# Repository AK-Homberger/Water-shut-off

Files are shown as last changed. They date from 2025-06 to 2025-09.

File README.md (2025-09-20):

# Water leakage detection and shut-off with ZigBee and ioBroker

A water damage following a burst pipe or other leak is always unpleasant. Especially when it happens while you're on vacation and no one notices the damage, but the water just keeps flowing. A simple project to shut off the house's water supply when a leak is detected can help. The detection is done with the Ikea BADRING water detector, and the shut-off is done with a 12-volt cordless screwdriver controlled by an Ikea TRETAKT switch. I implemented the logic and alarm system using the ioBroker smart home system and the ZigBee software Zigbee2MQTT. ioBroker also sends notifications via email and calls to your mobile phone. 

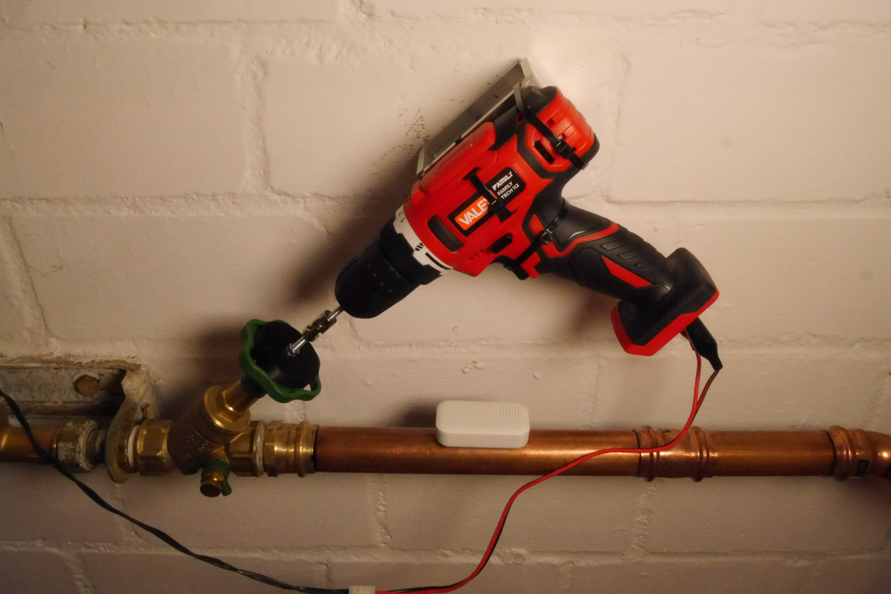
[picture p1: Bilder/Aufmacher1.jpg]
Shut-off


# Summary
- Domestic water shut-off via cordless screwdriver with torque adjustment 
- Leakage detection via Ikea ZigBee water detector BADRING 
- Control of the cordless screwdriver via Ikea ZigBee switch TRETAKT 
- Any number of sensors can be integrated 
- Adapter plate for handwheel as 3D printing template (customisable) 
- Cardan joint as axis shift compensation 
- Alerts via email and phone call (requires Fritzbox) 
- Control via script in IoBroker on a Raspberry 
- ZigBee integration in ioBroker via Zigbee2MQTT 

# Hardware
For the mechanical shut-off of the domestic water, I use a simple 12-volt hand drill with a torque setting. I had initially considered using a gear motor. But I couldn't find the necessary torque clutch anywhere at a reasonable price. It's standard on cordless drills, however. The [list of parts](https://github.com/AK-Homberger/Wasserabschalter/blob/main/README.md#sources) includes a link to [Amazon](https://www.amazon.de/Akkuschrauber-Lithium-family-tech-112-Valex-1429400/dp/B077YSQW1Z). A simple drill for less than €20 is sufficient here.

Here is a short [video](https://www.dropbox.com/scl/fi/2sde03j0u3wew94bmh6hg/Abschalter.mov?rlkey=7kxjaejoa726u7x39rb6fkuw9&dl=0), that shows the function.

The drill is connected to the water valve's handwheel via a universal joint and an adapter plate. The universal joint is designed to compensate for slight axis shifts. It would probably work without this joint as well.

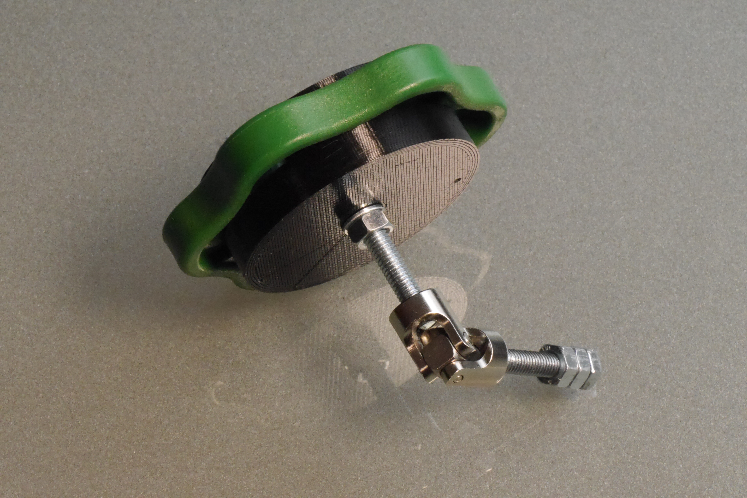
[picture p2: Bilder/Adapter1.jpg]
Adapter


The adapter plate and mounting ring are available in the SCAD directory as OpenSCAD and STL files. The adapter plate should fit for most handwheels. However, if necessary, the plate can easily be adapted to the current handwheel using [OpenSCAD](https://openscad.org/). 

Adapter plate / Ring

### Important! Non-rising spindle
The shut-off only works with valves with a ["non-rising"](https://www.youtube.com/watch?v=0fCbAA_am2k) spindel/stem. With valves with a "rising" spindle, the handwheel shaft rotates into the valve when shutting off. This would cause the distance to the drill to steadily increase until there is no longer any connection. Therefore, check beforehand whether a valve with a "non-rising" spindle is installed. The valves/upper parts can also be easily replaced. Your local plumber can help with this if necessary.

To easily mount the cordless screwdriver, I use so-called [Thermohalter](https://alufensterbaenke.de/thermohalter) for window sills.

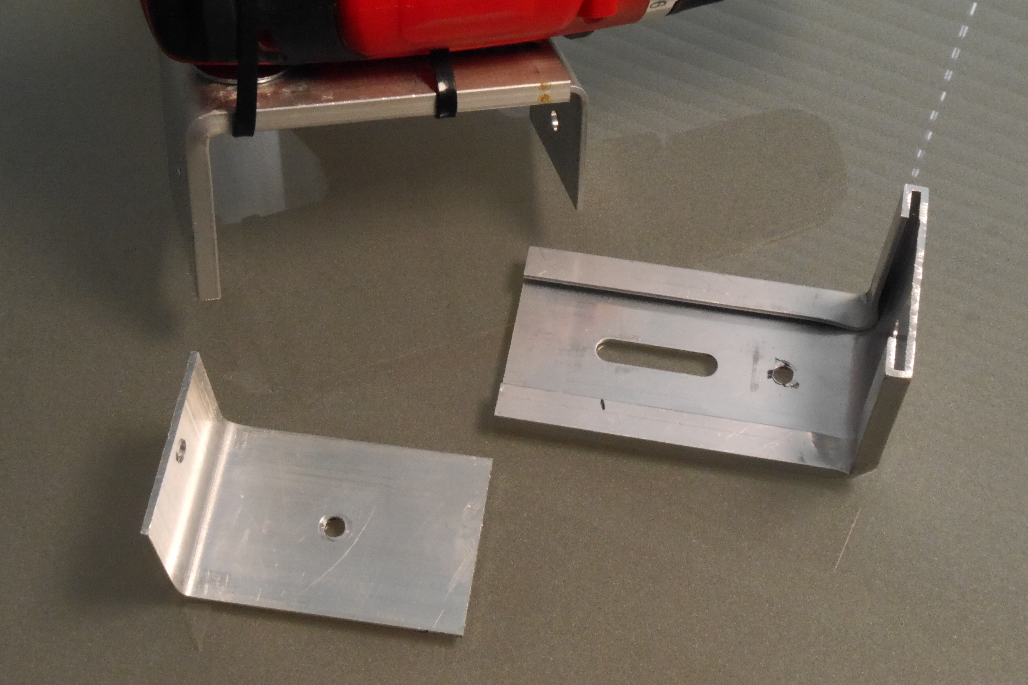
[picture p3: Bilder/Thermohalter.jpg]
Halter


Simply slide two of these brackets together to create a square box. The advantage of this solution is the variable distance from the wall, which can be easily adjusted by shortening the aluminum profiles to the required length. 

# Software
The water shut-off switch is controlled using a Raspberry Pi and two software components: the [ioBroker](https://www.iobroker.net/) smart home system and the [Zigbee2Mqtt](https://github.com/Koenkk/zigbee2mqtt) software. ioBroker handles automation via script, and Zigbee2Mqtt connects the Ikea ZigBee components TRETAKT (switch) and BADRING (leakage detector).

For reliable operation of the system, at least a Raspberry 4 with 2 GB of RAM is required. A complete bundle is available [here](https://www.reichelt.de/de/de/shop/produkt/das_reichelt_raspberry_pi_4_b_2_gb_all-in-bundle-263082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), for example.

## Installing Raspberry OS and ioBroker
To prepare the installation, you first need the "Raspberry Pi Imager," which is available for download [here](https://www.raspberrypi.com/software/).

As the operating system for ioBroker, I recommend the OSLite version for the Raspberry Pi without a graphical desktop. ioBroker and Zigbee2mqtt are operated via a browser. However, other versions of the operating system will also work.

For easy replication, I've listed all the commands here. They can be copied and pasted into the Raspberry Terminal.

Before installing the software, the [Sonoff ZigBee-Adapter](https://sonoff.tech/product/gateway-and-sensors/sonoff-zigbee-3-0-usb-dongle-plus-p/) should be plugged into a USB port.

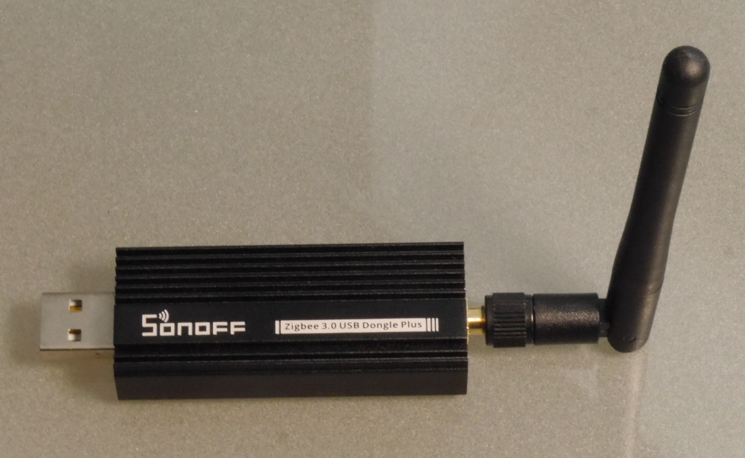
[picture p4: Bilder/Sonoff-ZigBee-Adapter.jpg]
Sonoff-Dongle


Important: There are two versions of the ZigBee adapter, SBDongle-P and ZBDongle-E, with different chipsets. For this project, the "P" dongle with the "CC2652P" chipset is required. The other version should also work. However, some configuration settings will need to be changed.

For a better wireless connection, it has proven useful not to plug the dongle directly into the Raspberry, but to place it some distance away from the Raspberry using a USB extension cable.

## Installation

- Start Rapberry Imager as administrator (at least under Windows 11; otherwise, the antivirus will block copying of some components)
- Select 64-bit OSLite
- Set hostname and password
- Select SD card and write image
- Insert SD card into Raspberry and start
- Log in. Either locally with keyboard and screen or via SSH. Find out the IP address via the router! I recommend using [Putty](https://putty.org/index.html) as an SSH client.

Update Raspberry OS first:
```
sudo apt update
sudo apt upgrade

sudo raspi-config - Filesystem expand und Logging aus.
```

Install ioBroker with: 
```
curl -sLf https://iobroker.net/install.sh | bash - 
```

Open ioBroker in your browser: http://IP-Adresse:8081

Set basic ioBroker settings. Do not run Discover.

Install the following adapters in ioBroker:
- Email
- Javascript
- Tr-064
- Zigbee2Mqtt

To do this, simply search for the adapter names and install and configure the instance using "Info" (three dots icon) and "+." To change the configuration, go to "Instances" and select the wrench icon.

Configure zigbee2mqtt.0:
For "Websocket IP Address" and "WebUi Address" specify the Raspberry's own IP address (command "ifconfig" helps).
Select "Create a dummy MQTT server for Zigbee2MQTT" and specify port "1887." Leave the other settings as they are and save.

## Installation Zigbee2Mqtt

Detailed information can be found here: https://www.zigbee2mqtt.io/guide/installation/01_linux.html

However, the following commands are sufficient:
```
sudo curl -fsSL https://deb.nodesource.com/setup_lts.x | sudo -E bash -
sudo apt install -y nodejs git make g++ gcc libsystemd-dev
sudo npm install -g pnpm

sudo mkdir /opt/zigbee2mqtt
sudo chown -R ${USER}: /opt/zigbee2mqtt

git clone --depth 1 https://github.com/Koenkk/zigbee2mqtt.git /opt/zigbee2mqtt

cd /opt/zigbee2mqtt
pnpm i --frozen-lockfile
```

Adjust the "configuration.yaml" file: 

```
nano /opt/zigbee2mqtt/data/configuration.yaml
```
Insert the following text: 
```yaml
homeassistant:
  enabled: false
frontend:
  enabled: true
  port: 8080
  host: 0.0.0.0
mqtt:
  base_topic: zigbee2mqtt
  server: mqtt://localhost:1887
serial:
  port: /dev/ttyUSB0
  adapter: zstack
advanced:
  cache_state: false
  output: json
  channel: 11
  transmit_power: 5
  homeassistant_legacy_entity_attributes: false
  homeassistant_legacy_triggers: false
  legacy_api: false
  legacy_availability_payload: false
  log_level: warning
device_options:
  legacy: false
availability:
  enabled: true
  active:
    timeout: 10
  passive:
    timeout: 1500
```
Exit with Ctrl-X and write with "Y".

Test with:
```
pnpm start
```
Cancel execution with Ctrl-C.

Start as a service:

Start the editor and create the file "zigbee2mqtt.service" with the following content.

```
sudo nano /etc/systemd/system/zigbee2mqtt.service
```
Insert the following text: 
```service
[Unit]
Description=zigbee2mqtt
After=network.target

[Service]
Environment=NODE_ENV=production
#Type=notify
ExecStart=/usr/bin/node index.js
WorkingDirectory=/opt/zigbee2mqtt
StandardOutput=inherit
#Or use StandardOutput=null if you don't want Zigbee2MQTT messages filling syslog, for more options see systemd.exec(5)
StandardError=inherit
#WatchdogSec=10s
Restart=always
RestartSec=10s
User=pi

[Install]
WantedBy=multi-user.target
```
Exit with Ctrl-X and write with "Y". Due to missing components in my Raspberry version (Bookworm), I had to comment out:
```
#Type=notify
```
and
```
#WatchdogSec=10s
```
Otherwise, starting via Systemctl didn't work properly (crashes). Other users have also encountered this [error](https://github.com/Koenkk/zigbee2mqtt/issues/21463). 

Now start the service and check status. If status OK enable automatic start after re-boot.
```
sudo systemctl start zigbee2mqtt
systemctl status zigbee2mqtt.service
sudo systemctl enable zigbee2mqtt.service
```
Now the Raspberry can be restarted with "sudo reboot".

Open ioBroker in your browser: http://IP-Adresse:8081

Then switch to the Zigbee2MQTT tab and add the [TRETAKT](https://www.zigbee2mqtt.io/devices/E22x4.html#ikea-e22x4) switch and at leats one leakage sensor [BADRING](https://www.zigbee2mqtt.io/devices/E2202.html#ikea-e2202). 

Tretakt
Badring

To do this, select "Permit join (all)". For the TRETAKT switch, the small button in the recess below the power button must be pressed for approximately 2 seconds to pair. For the BADRING sensor, the pairing button is located under the battery cover. The button must be pressed four times in succession.

The components should now appear in the list.

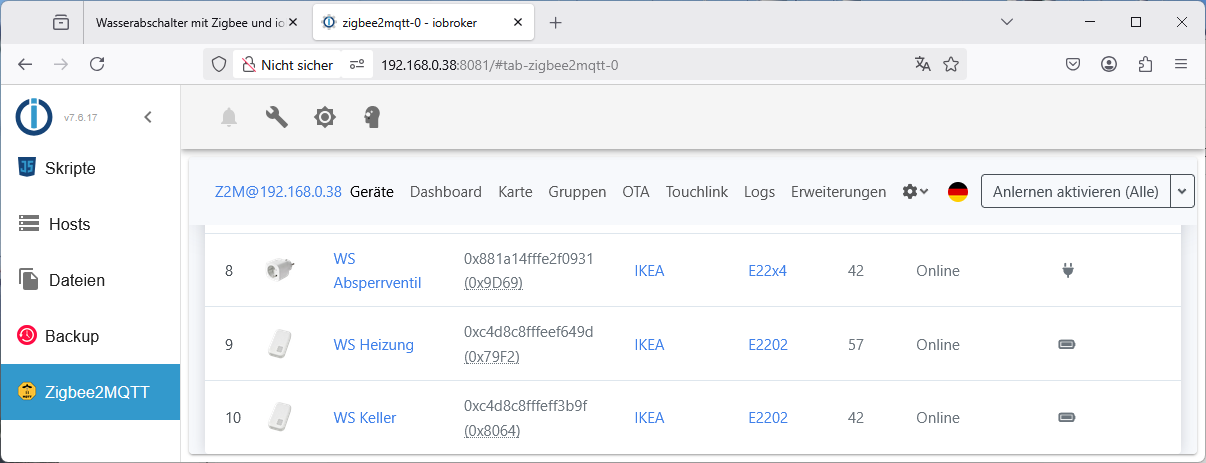
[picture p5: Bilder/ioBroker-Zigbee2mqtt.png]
Z2M


In the next step we create the script to control the cordless screwdriver and for notification.

To do this, select "Scripts" in the ioBroker menu on the left, create a new script with "+" and click "JS" for JavaScript. Name it "Water Switch." Then insert the following text:

```javascript
var OffTime = 3; // Zeit zum Abdrehen in Sekunden

var Schalter = "zigbee2mqtt.0.0x881a14fffe2f0931.state";
var Sensor_1 = "zigbee2mqtt.0.0xc4d8c8fffeef649d.detected";
var Sensor_2 = "zigbee2mqtt.0.0xc4d8c8fffeff3b9f.detected";

// Motor ausschalten
function AbschaltungAus() {
    setState(Schalter, false);    
}

// Motor für "OffTime" einschalten
function AbschaltungAn() {
    setState(Schalter, true);
    setTimeout(AbschaltungAus, OffTime * 1000);	
}

AbschaltungAus();  // Abschalten beim Start des Scripts

// Heizung Sensor (Therme und Speicher)
on({id: Sensor_1}, async function (obj) {
          
    if (getState(Sensor_1).val == true) {
	    AbschaltungAn();
        sendTo("email.0", "Wassersensor Heizung: Feucht!"); // Sende email 
        setState("tr-064.0.states.ring", "Telefonnummer");    // Anrufen            
    }    
    else if (getState(Sensor_1).val == false) {
		sendTo("email.0", "Wassersensor Heizung: Trocken!");// Sende email         
    }    
});

// Keller Sensor
on({id: Sensor_2}, async function (obj) {
          
    if (getState(Sensor_2).val == true) {
	    AbschaltungAn();
        sendTo("email.0", "Wassersensor Keller: Feucht!");  // Sende email 
        setState("tr-064.0.states.ring", "Telefonnummer");    // Anrufen             
    }    
    else if (getState(Sensor_2).val == false) {
		sendTo("email.0", "Wassersensor Keller: Trocken!"); // Sende email       
    }    
});

// Abschaltung nach "OffTime" nach manuellem Anschalten zum Testen (Sensoren trocken)
on({id: Schalter}, async function (obj) {
          
    if ((getState(Schalter).val == true) && 
        (getState(Sensor_1).val == false) &&
        (getState(Sensor_2).val == false)) {
	    setTimeout(AbschaltungAus, OffTime * 1000);
    }             
});
```

The unique names of the ZigBee components "Switch" and "Sensor_1/2" still need to be adjusted in the script. The correct names can be found and inserted using the "Insert Object ID" function with the clipboard icon in the top right corner. The "Phone Number" also needs to be adjusted.
Then select "Save." As long as no error messages appear, you can test it. Incidentally, the leak sensor also reacts to wet fingers.
When triggered, the water should be turned off and an email should be sent. If a Fritzbox is present, the phone with the specified number should also ring. If no Fritzbox is present, please comment out the lines "setState("tr-064.0.states.ring", "Telephone number");".

# Sources:

- Raspberry Pi 4 Kit [Reichelt.de](https://www.reichelt.de/de/de/shop/produkt/das_reichelt_raspberry_pi_4_b_2_gb_all-in-bundle-263082)
- SONOFF Zigbee 3.0 USB Dongle [Amazon.com](https://www.amazon.de/SONOFF-Gateway-CC2652P-Assistant-Zigbee2MQTT/dp/B09KXTCMSC)
- Ikea Zigbee switch TRETAKT [Ikea](https://www.ikea.com/de/de/p/tretakt-steckdose-smart-80540349/)
- Ikea Zigbee leakage sensor BADRING [Ikea](https://www.ikea.com/de/de/p/badring-wasserlecksensor-smart-60504352/)
- Cordless screwdriver [Amazon.com 1](https://www.amazon.de/Akkuschrauber-Lithium-family-tech-112-Valex-1429400/dp/B077YSQW1Z) / [Amazon.com 2](https://www.amazon.de/Akkuschrauber-Bohrschrauber-Akkubohrer-Bohrfutter-Drehmomenteinstellung/dp/B0DP2GMW69)
- Thermohalter (2 pieces) [Alufensterbaenke.de](https://alufensterbaenke.de/thermohalter)
- Cardan joint [Amzon.com](https://www.amazon.de/bis-Durchmesser-drehbar-Kardangelenk-RC-Modellflugzeug/dp/B00O9YGCKU)
- 12 Volt 10 A Trafo [Amazon.com](https://www.amazon.de/Netzteil-Spannungswandler-Netzadapter-Transformator-Stromversorgung-schwarz/dp/B0D9S8N8TT)
- Clips [Amazon.com](https://www.amazon.de/Multimeter-Messleitungen-Bananenstecker-Krokodilklemme-Messspitzen/dp/B0D39WQZ9M)

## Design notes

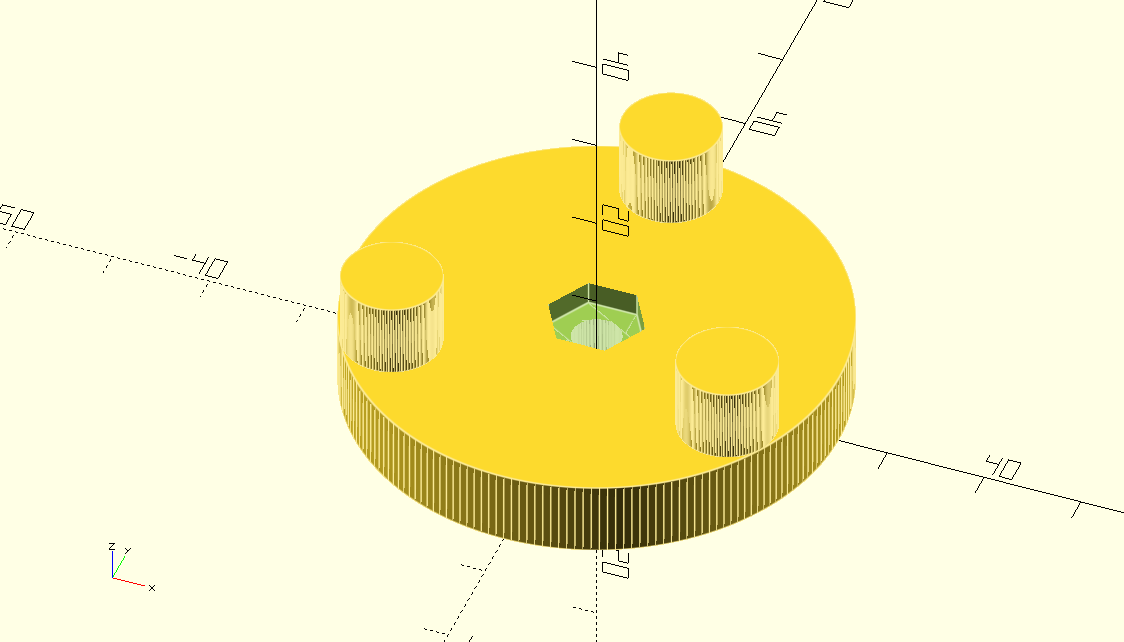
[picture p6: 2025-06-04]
Bilder/Adapterplatte.png

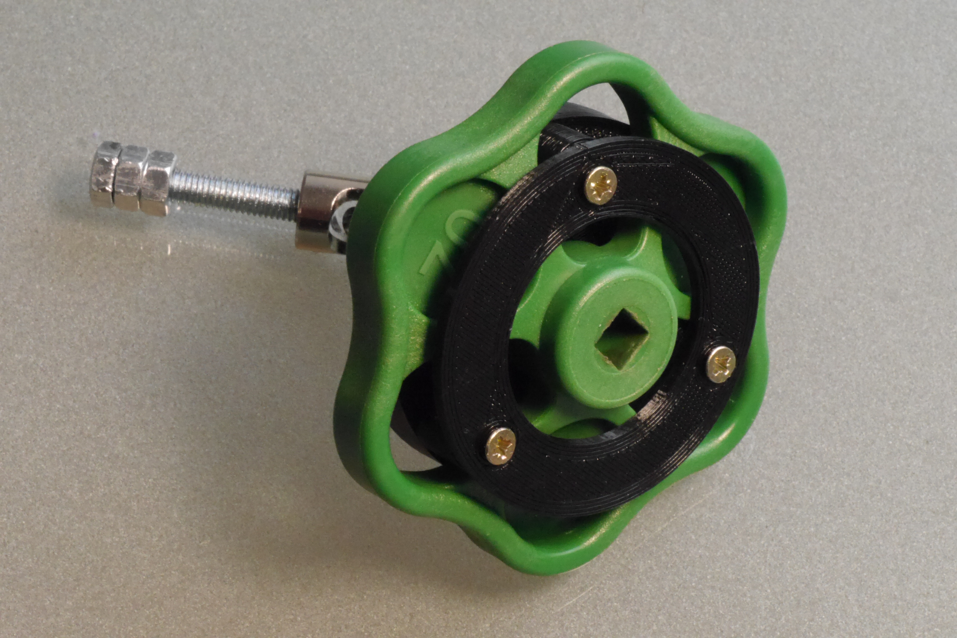
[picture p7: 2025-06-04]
Bilder/Adapter2.jpg

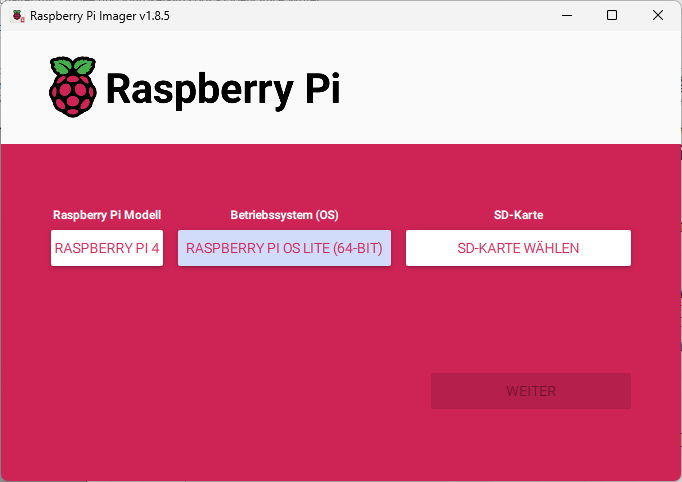
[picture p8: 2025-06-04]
Bilder/RaspberryPiImager.png

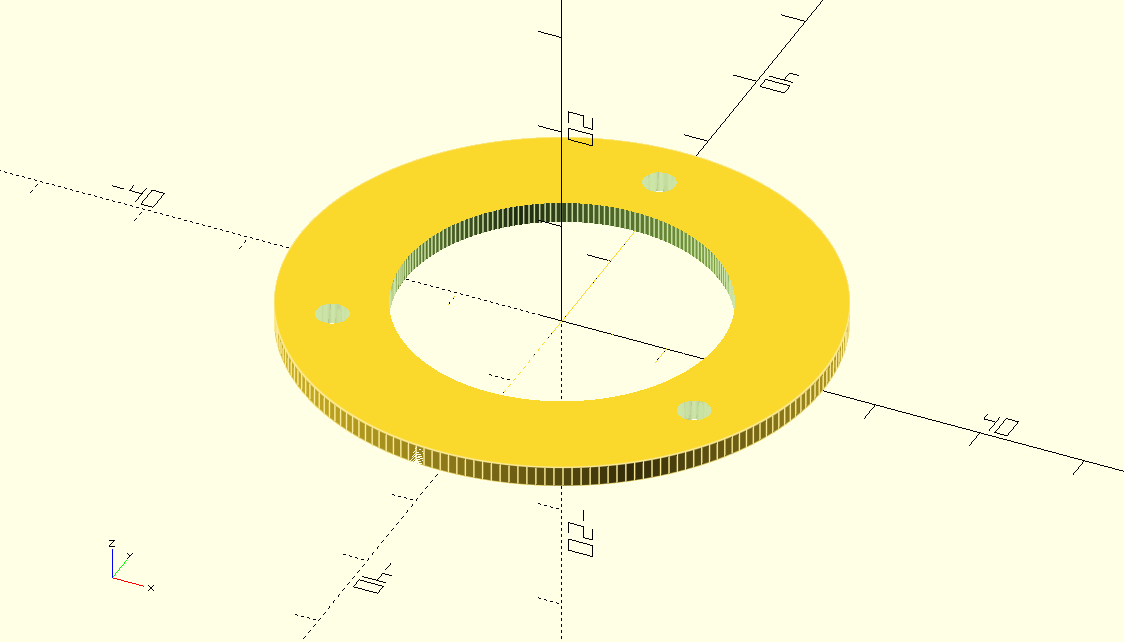
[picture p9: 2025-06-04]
Bilder/Befestigungsring.png

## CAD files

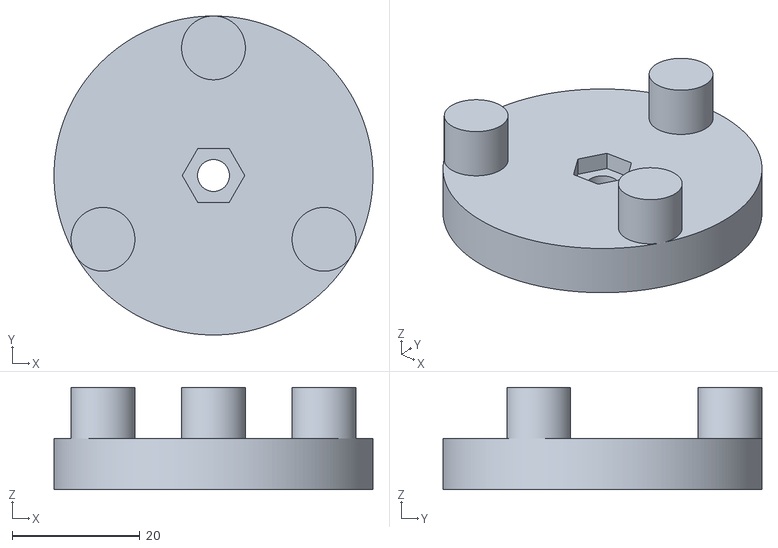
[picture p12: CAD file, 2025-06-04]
SCAD/Adapterplatte.stl
50.0 x 50.0 x 16.0

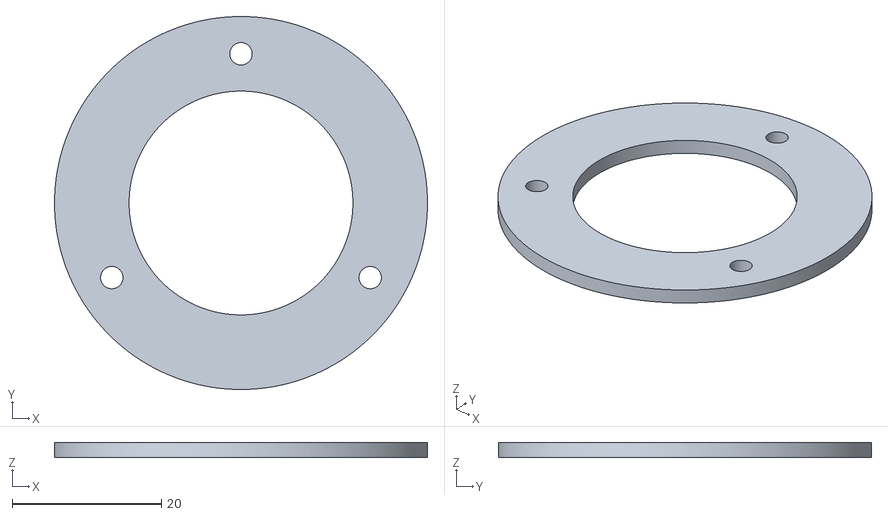
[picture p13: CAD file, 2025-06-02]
SCAD/Befestigungsring.stl
50.0 x 50.0 x 2.00

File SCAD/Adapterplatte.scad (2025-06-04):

// Runde Grundplatte
highth = 8;
diameter = 50;

// Sechskannt-Aussparung
highth2 = 5.5;
width = 4.9;
hole = 5;

// Zapfen
pin = 10;
hole_distance = 20;
highth3 = 8;



difference(){
    
    cylinder(highth, r1 = diameter/2, r2 = diameter/2, $fn=200);    
    translate ([0, 0, -1]){
    cylinder(highth+2, r1 = hole/2, r2 = hole/2, $fn=200);  
    }
    translate ([0, 0, highth]){
        hexagon(width, highth2, true);
        
    }
}

translate ([0, hole_distance, highth]){
   cylinder(highth3, r1 = pin/2, r2 = pin/2, $fn=200);  
}
   
rotate([0, 0, 120])


translate ([0, hole_distance, highth]){
    cylinder(highth3, r1 = pin/2, r2 = pin/2, $fn=200);  
    
}

rotate([0, 0, 240])

translate ([0, hole_distance, highth]){
    cylinder(highth3, r1 = pin/2, r2 = pin/2, $fn=200);  
}


module hexagon(side, height, center) {
  length = sqrt(3) * side;
  translate_value = center ? [0, 0, 0] :
                             [side, length / 2, height / 2];
  translate(translate_value)
    for (r = [-60, 0, 60])
      rotate([0, 0, r])
        cube([side, length, height], center=true);
}


module hexagon_inscribed(radius, height, center) {
  hexagon(2 * radius / sqrt(3), height, center);
}

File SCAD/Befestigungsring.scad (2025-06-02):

highth = 2;
diameter = 50;
hole_distance = 20;
gap = 3;


difference(){
    
    cylinder(highth, r1 = diameter/2, r2 = diameter/2, $fn=200); 
    
    translate ([0, 0, -1])
    cylinder(highth+2, r1 = diameter/2-10, r2 = diameter/2-10, $fn=200);    
    
    translate ([0, hole_distance, -1]){
    cylinder(highth+2, r1 = gap/2, r2 = gap/2, $fn=200);  
    }
    
    rotate([0, 0, 120])
    translate ([0, hole_distance, -1]){
        cylinder(highth+2, r1 = gap/2, r2 = gap/2, $fn=200);  
  
    }

     rotate([0, 0, 240])
     translate ([0, hole_distance, -1]){
        cylinder(highth+2, r1 = gap/2, r2 = gap      /2, $fn=200);  
    }


}

   
